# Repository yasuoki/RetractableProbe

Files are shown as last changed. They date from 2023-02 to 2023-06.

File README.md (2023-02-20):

# Retractable probe built into X-carriage
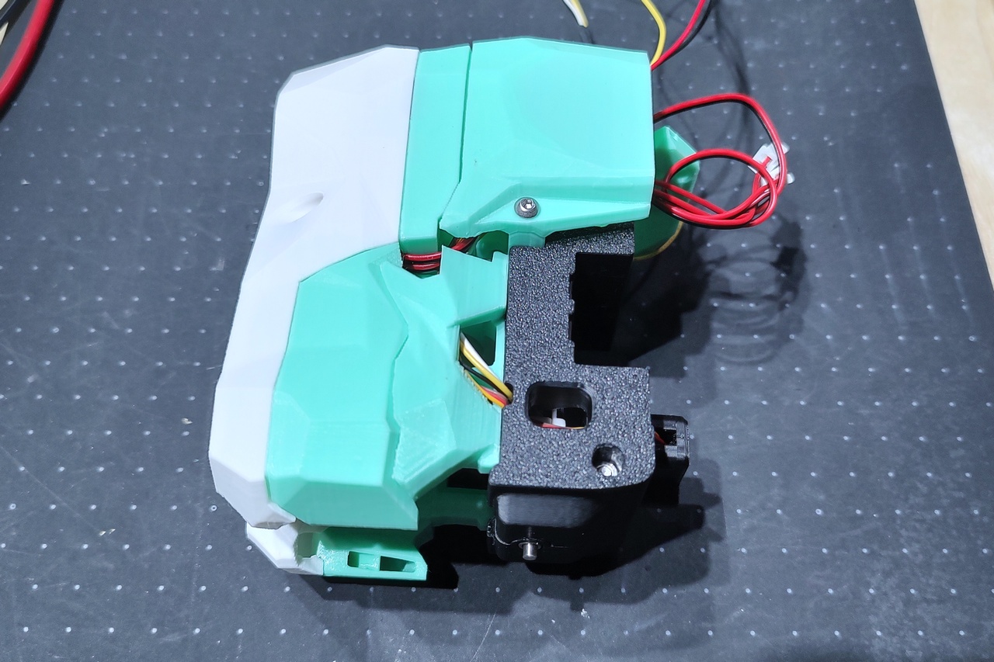
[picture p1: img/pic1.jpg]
<br>

(https://www.youtube.com/watch?v=CPbT1QPZcho)

The retractable probe of the Strix toolhead has been miniaturized and integrated into the X-carriage.  
The project features the following.

- Fits MGN12 X-rail only
- Replaces OMRON TL-Q5MC, which has concerns about heat resistance.
- Same size as the genuine VORON X-Carriage, so AfterBurner and StealthBurner can be used.
- Same weight as the genuine VORON X-Carriage with OMRON TL-Q5MC.
- Robust electrical circuits with no magnet-dependent electrical contacts.
- The accuracy of the probe depends only on the accuracy of the microswitch and not on the servomotor or spring.

# Caution
This probe is still under development and has not yet been tested for stability.   
I am trying to design a better, but something could go wrong and your 3D printer could break.

# BOM
- M3 x 30mm SHCS x1
- M3 x 40mm SHCS x1
- M2x10 Self Tapping Screw x4
- M1.7 x 3mm Flat Head Screw x1 (for servo horn)
- M3 x 6mm Set Screw x1
- M3 Hexnut x2
- M3 Heat Set Inserts x4
- Piano wire 0.8mm(D) x 6mm(L) x1
- Sleeve Bearing(Oilless Bushings) 3mm(ID) x 5mm(OD) x 5mm(L) x4
- Stainless Steel Compression Spring 4mm(OD) x 0.4mm(RD) x 15mm(L) x1
- Stainless Steel Shaft 3mm(D) x 57mm(L) x1
- E-Clip 2.0~2.5mm(ID) x2
- Wire 32~36AWG
- Micro Switch (OMRON D2F-01F Low operating force 0.74 N) x1
- Servo Motor (Dspower DS-M005) x1

LED Options
- LED Blue 3mm x1
- LED Red 3mm x1
- Resistor 1/4W 330~2k ohms x2 (Resistance depends on circuit)

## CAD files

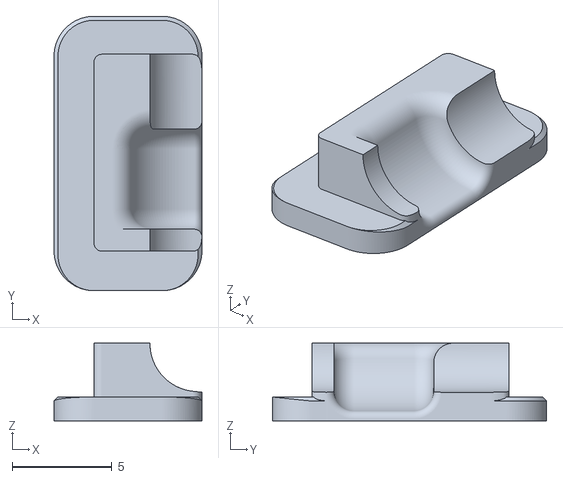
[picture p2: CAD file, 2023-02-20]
STLs/CableHoleLid.stl
7.40 x 13.7 x 3.89

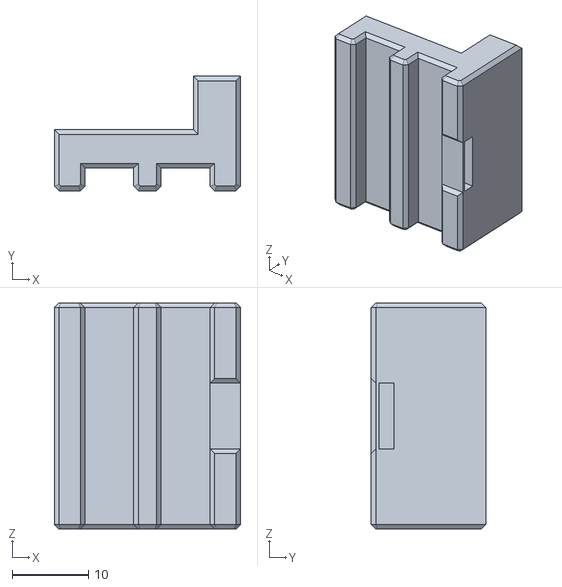
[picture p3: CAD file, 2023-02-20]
STLs/Tools/BeltGuideB_x2.stl
24.4 x 15.0 x 29.6

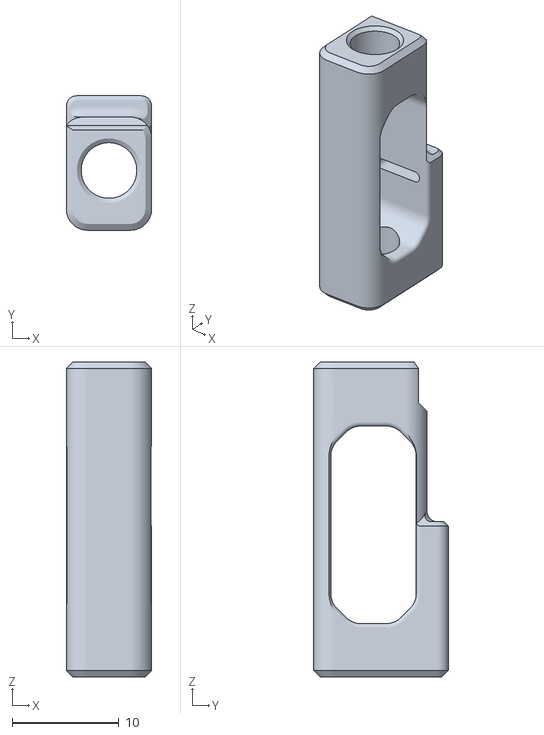
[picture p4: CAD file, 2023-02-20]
STLs/Elevator.stl
8.00 x 12.6 x 29.5

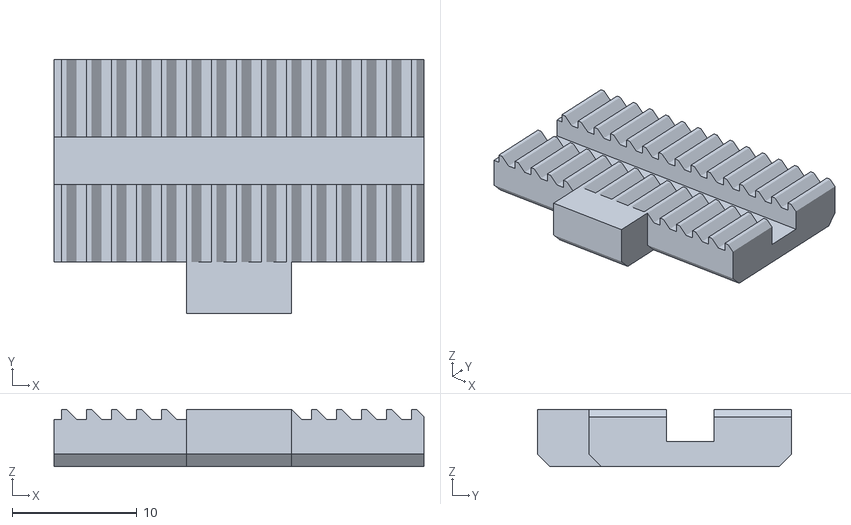
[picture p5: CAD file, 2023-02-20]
STLs/Tools/BeltGuideR.stl
29.6 x 20.3 x 4.60

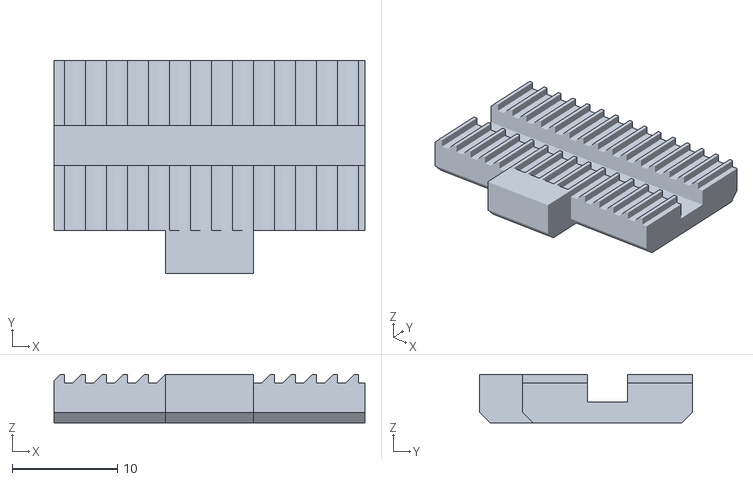
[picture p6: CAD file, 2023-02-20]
STLs/Tools/BeltGuideL.stl
29.6 x 20.3 x 5.00

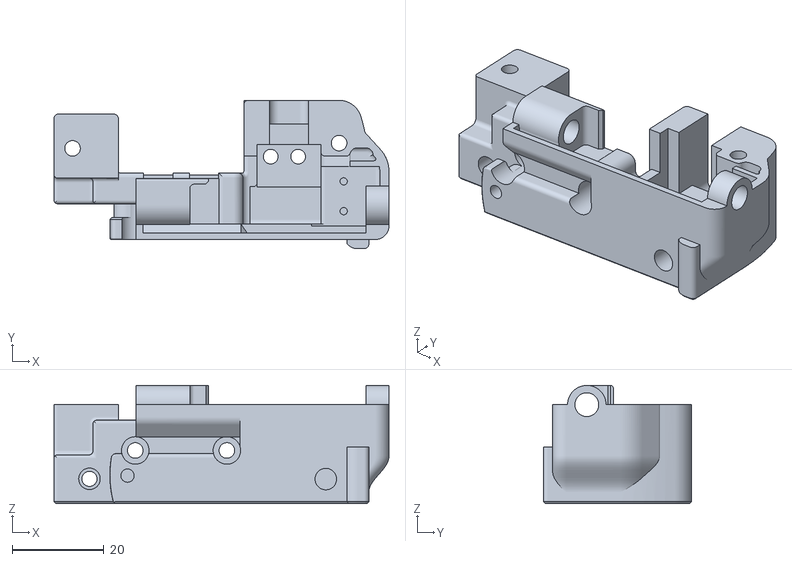
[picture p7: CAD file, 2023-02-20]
STLs/XCarriageLeft.stl
73.1 x 32.4 x 25.8

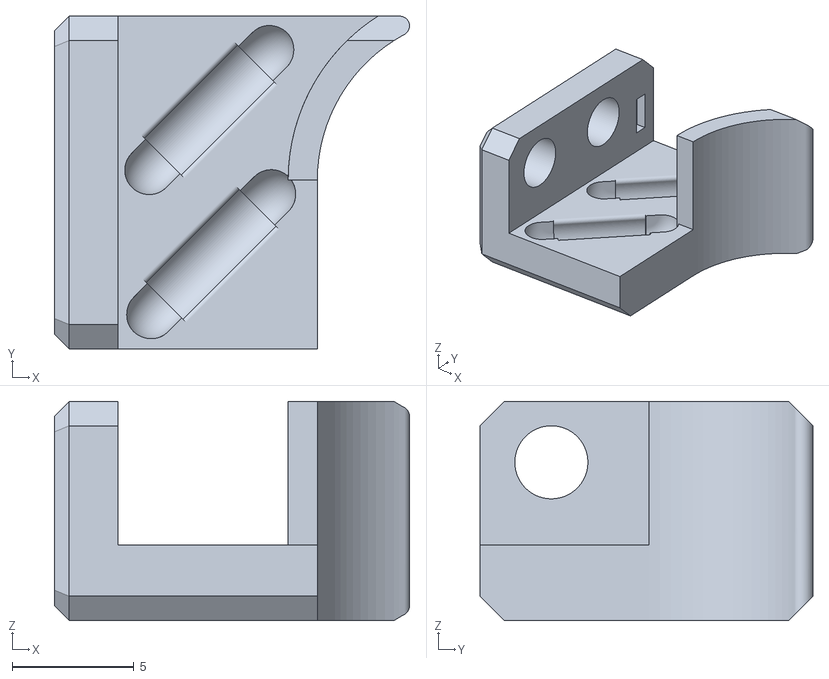
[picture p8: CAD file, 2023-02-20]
STLs/LedMount.stl
14.6 x 13.7 x 9.00

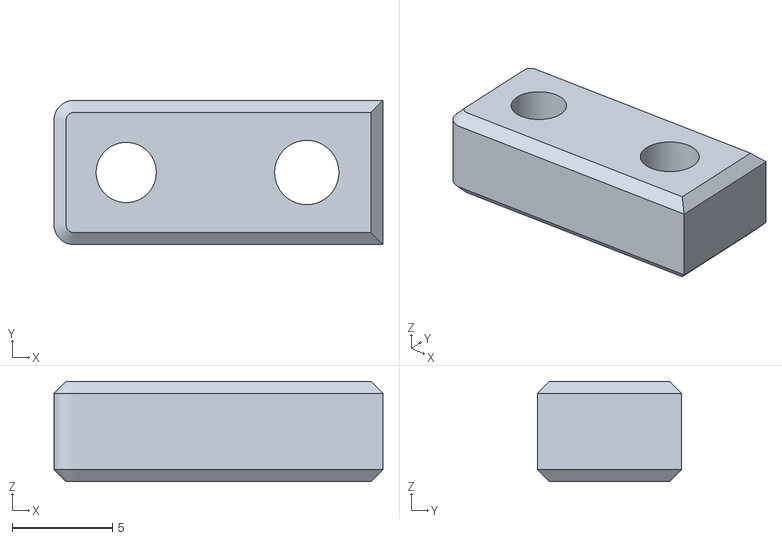
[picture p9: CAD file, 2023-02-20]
STLs/Trigger.stl
16.4 x 7.20 x 5.00

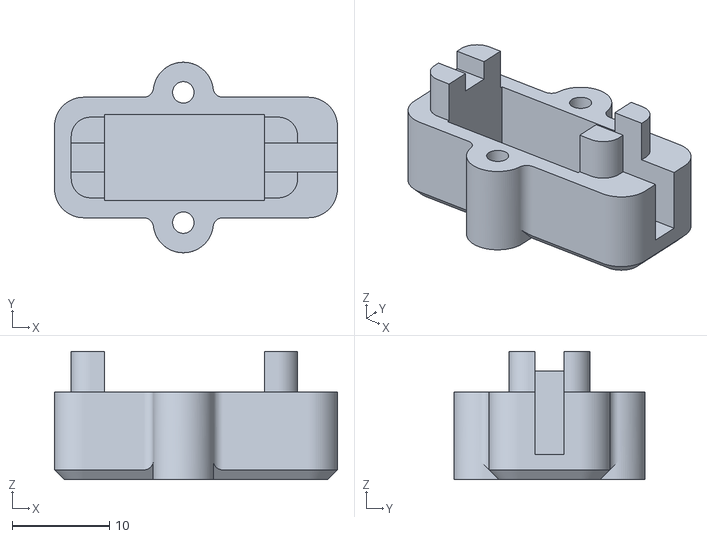
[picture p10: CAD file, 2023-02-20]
STLs/ServoCover.stl
29.1 x 19.6 x 13.2

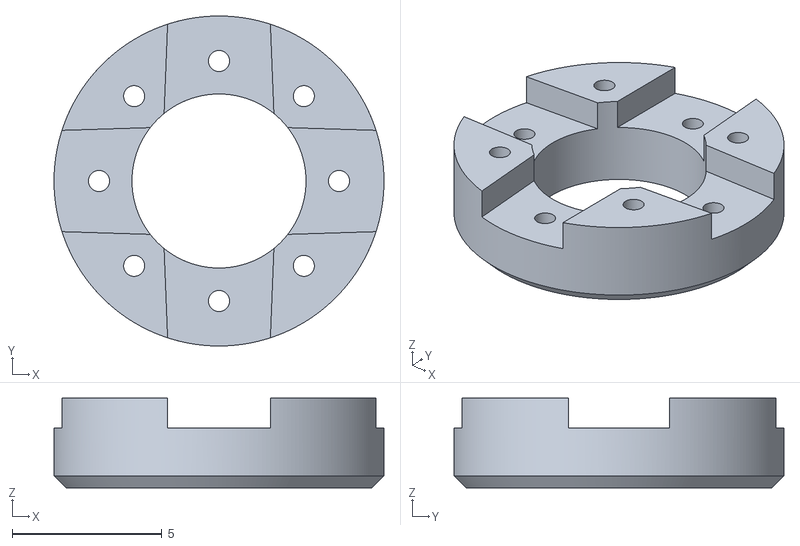
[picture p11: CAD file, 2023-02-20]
STLs/ServoHornA.stl
11.0 x 11.0 x 3.00

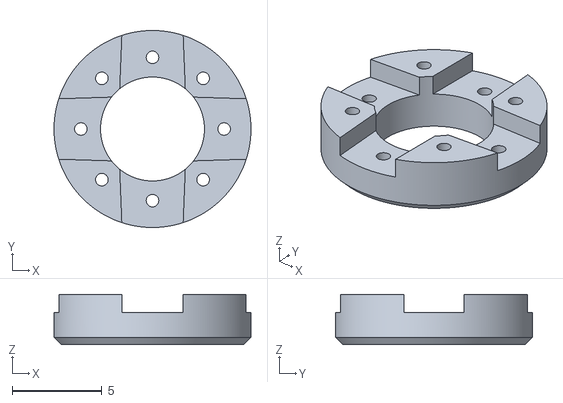
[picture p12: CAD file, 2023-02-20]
STLs/ServoHornB.stl
11.0 x 11.0 x 2.80

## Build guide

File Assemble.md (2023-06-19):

## Wiring for LEDs
This manual does NOT describe the wiring of LEDs.  
The reason is that additional circuitry and motherboard configuration are required to turn on the LEDs, and various configurations are possible depending on the individual printer environment.  
The design is intended to allow for LED installation, but it is not required. If you think it is necessary, please devise your own wiring.  
A simplified schematic is shown below, but the question is where to wire the 3.3V from?  
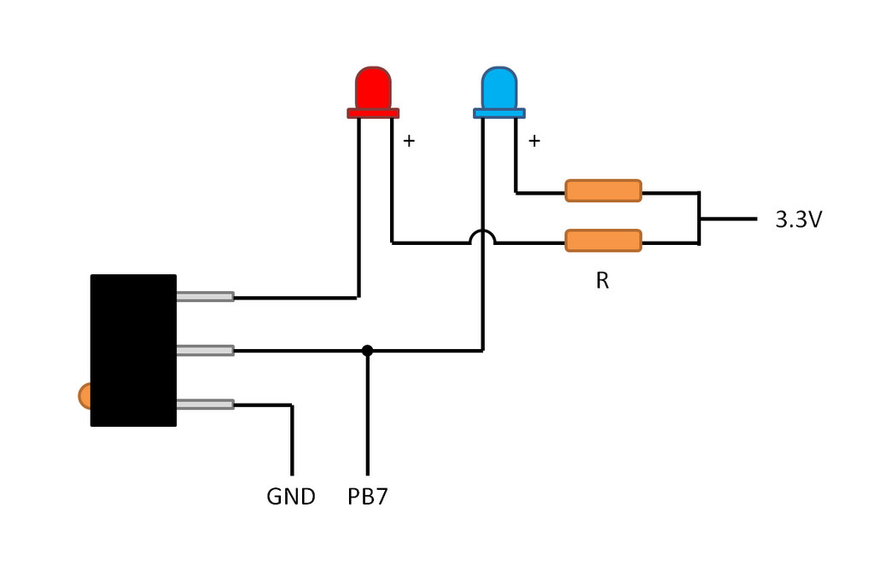
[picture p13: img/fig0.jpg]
<br>  
This 3.3V needs to be controllable by G-Code as I want to turn it on and off in conjunction with probe rod expansion and retraction.  
From what I have seen in the BTT Octopus schematic, it looks like the only PINs that can be used for such an application are probably Fan0-Fan5 (Fan6 and 7 cannot be used), or J37 for the Neopixel LED.  
Both PINs are 5v or higher, so to obtain 3.3V, either a step-down by regulator or leveling PWM output is required.  

## Parts Printing
Layer height 0.2mm, Extrusion width 0.4mm, Wall count 4, Top/Bottom layers 8, Infill 40%.  
All parts do not require support.  
Some parts have built-in supports, so remove them.  
ServoHornA.stl and ServoHornB.stl differ in thickness by 0.2 mm. Select the one that fits.  

## Assemble
Only procedures different from the VORON standard X-Cariagge are explained.  
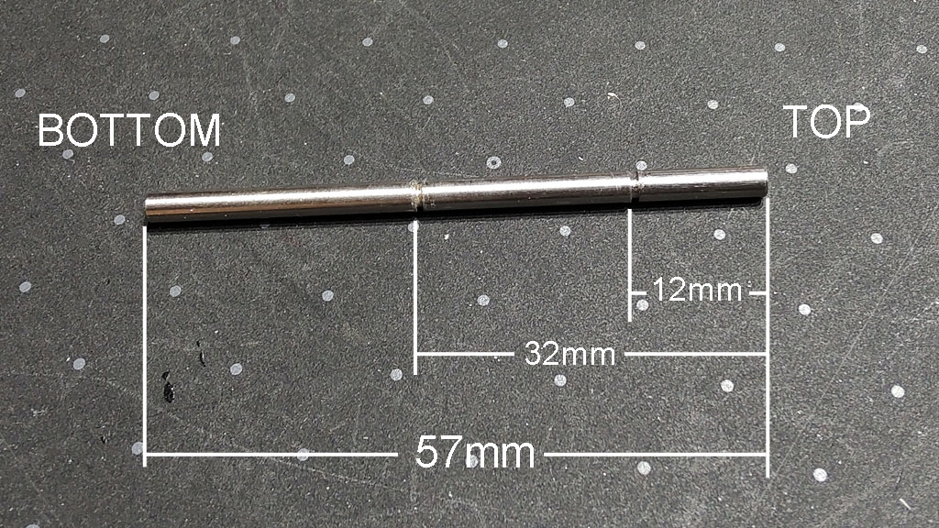
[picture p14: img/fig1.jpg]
<br>
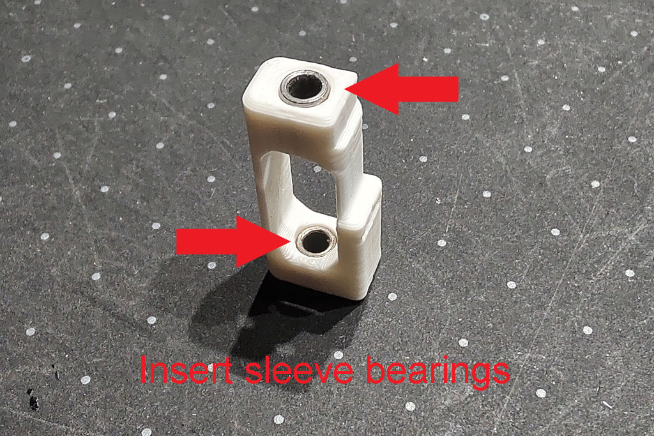
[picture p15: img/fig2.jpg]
<br>
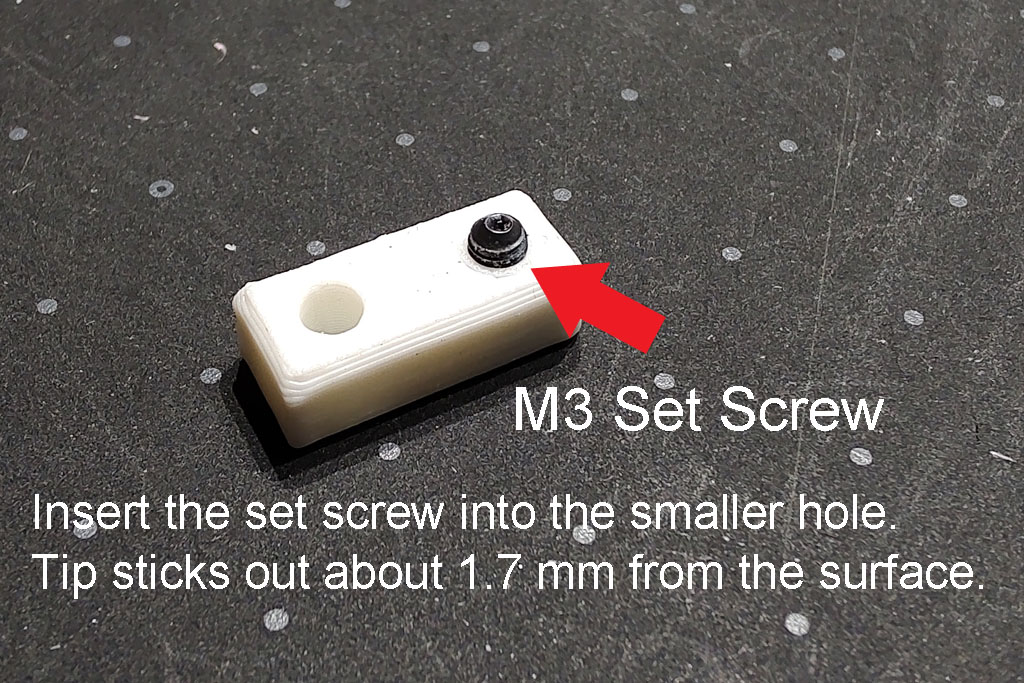
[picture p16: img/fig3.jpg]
<br>
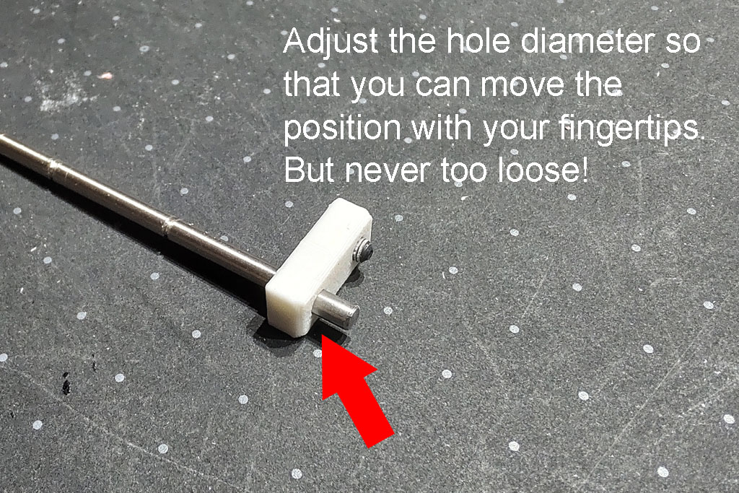
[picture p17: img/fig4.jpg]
<br>
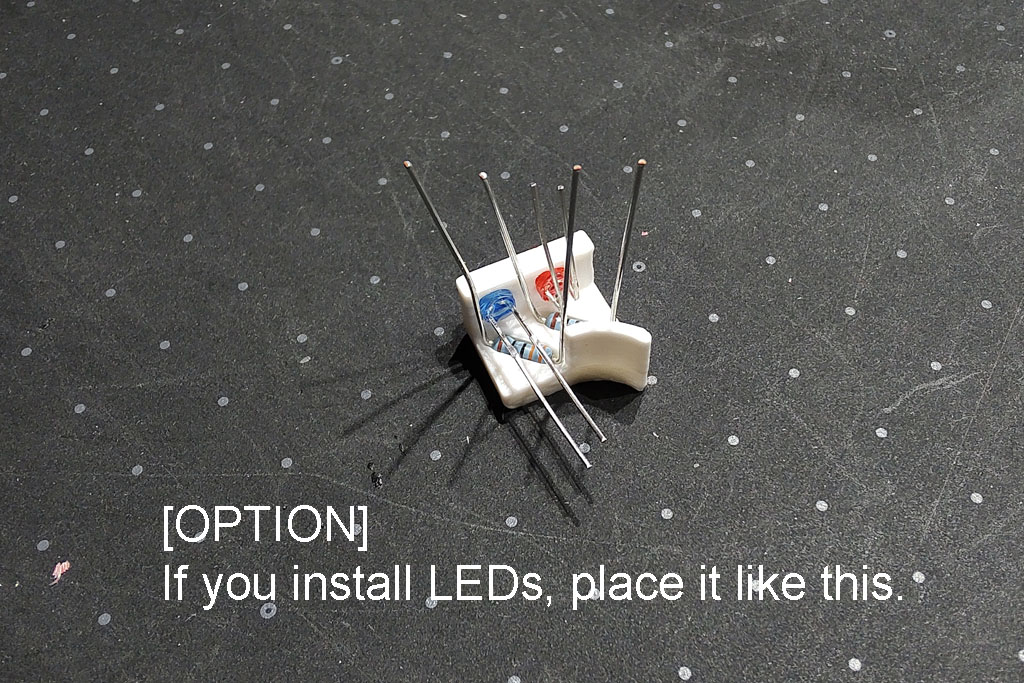
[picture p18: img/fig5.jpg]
<br>
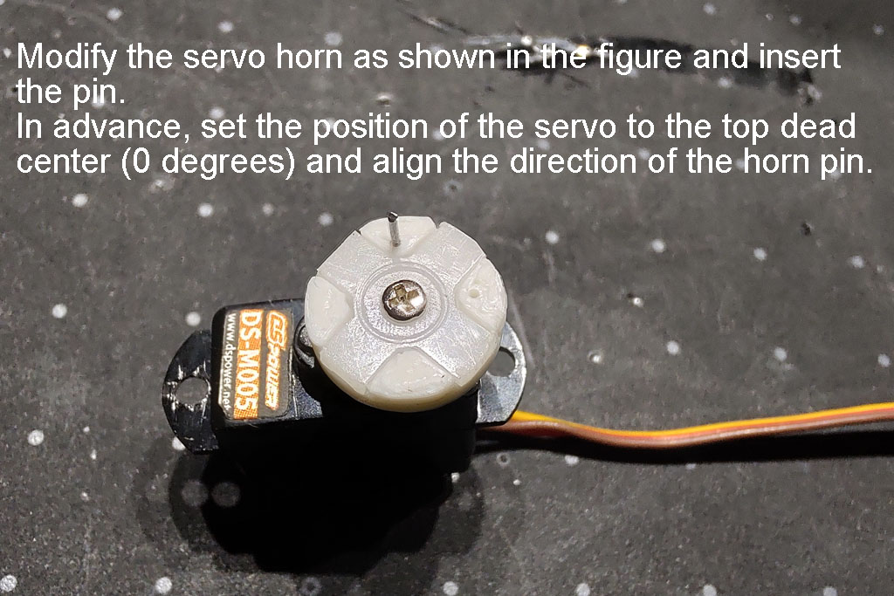
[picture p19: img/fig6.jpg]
<br>
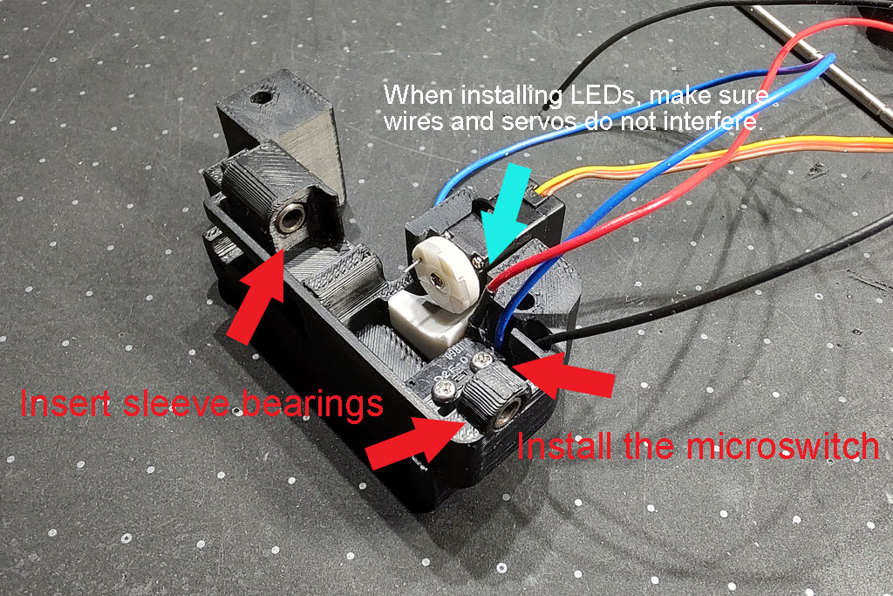
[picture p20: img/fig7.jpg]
<br>
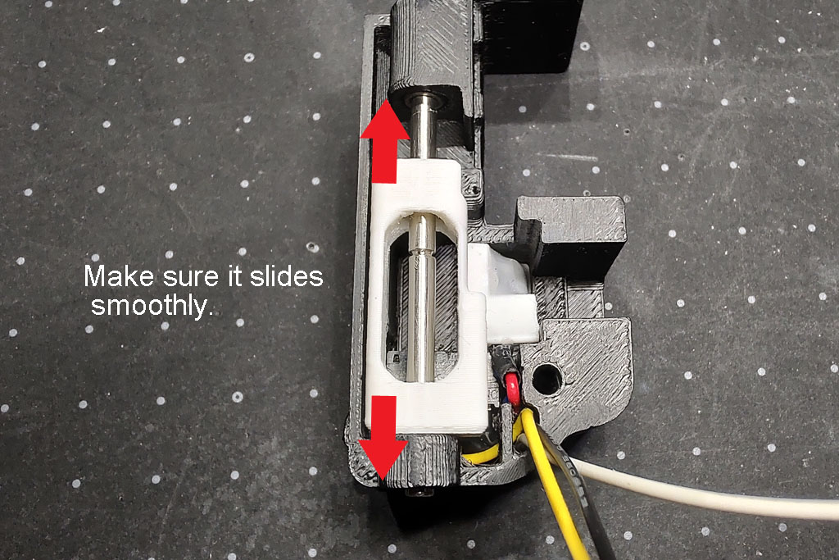
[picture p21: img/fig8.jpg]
<br>
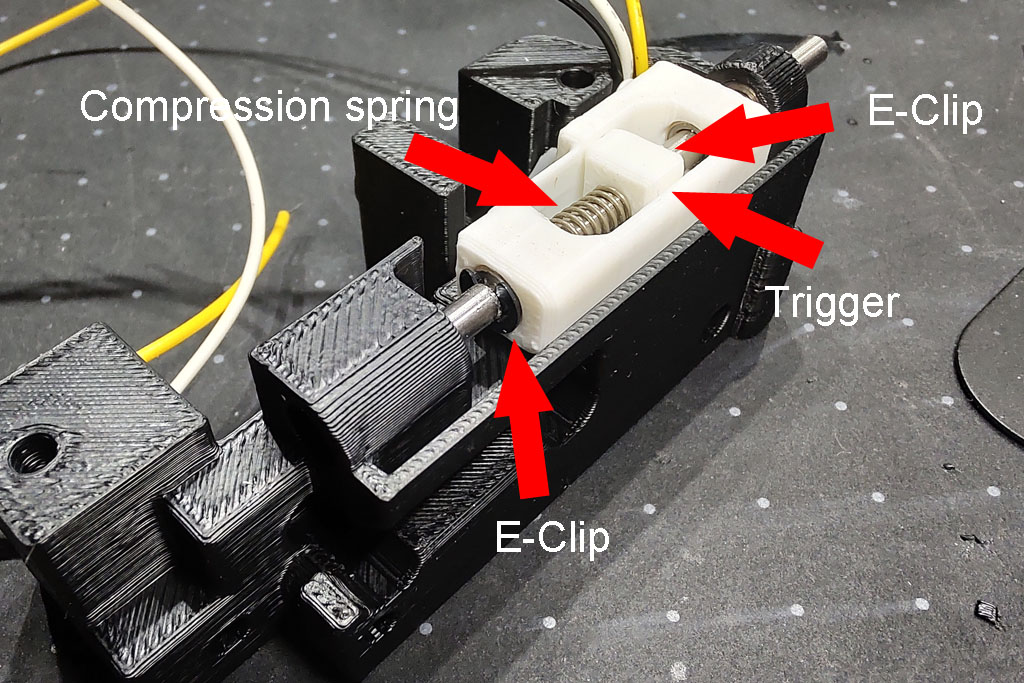
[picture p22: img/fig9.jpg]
<br>
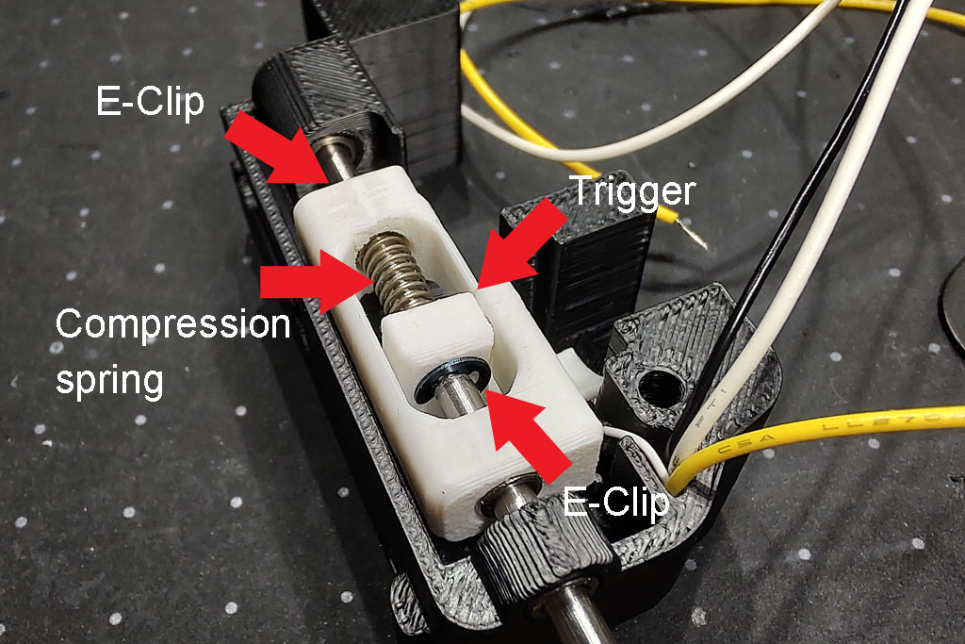
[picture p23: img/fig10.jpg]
<br>
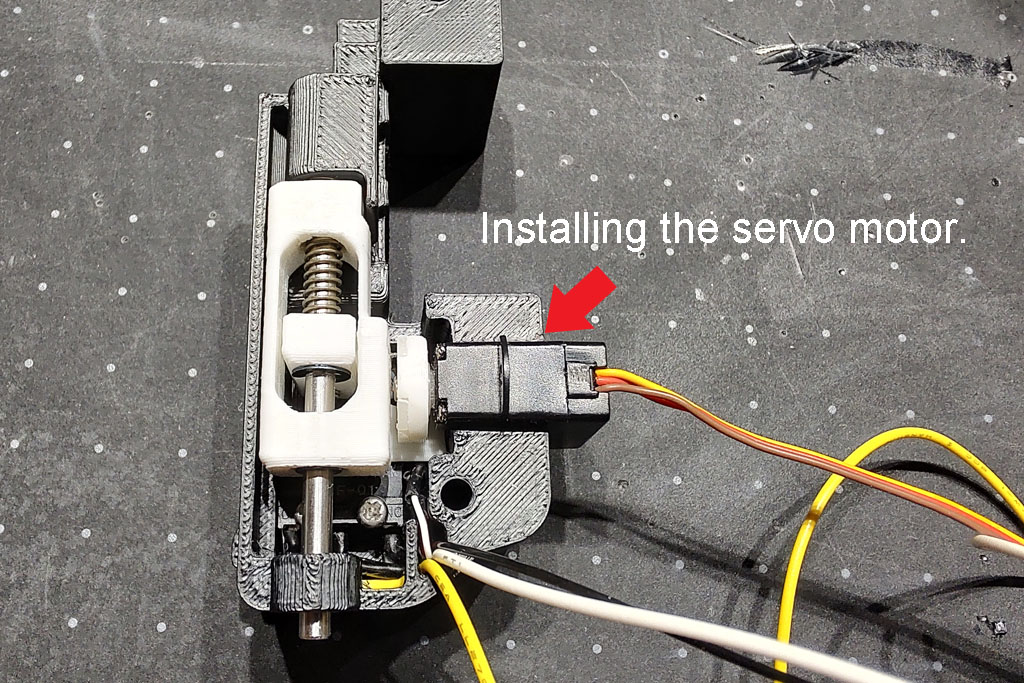
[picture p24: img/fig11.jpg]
<br>
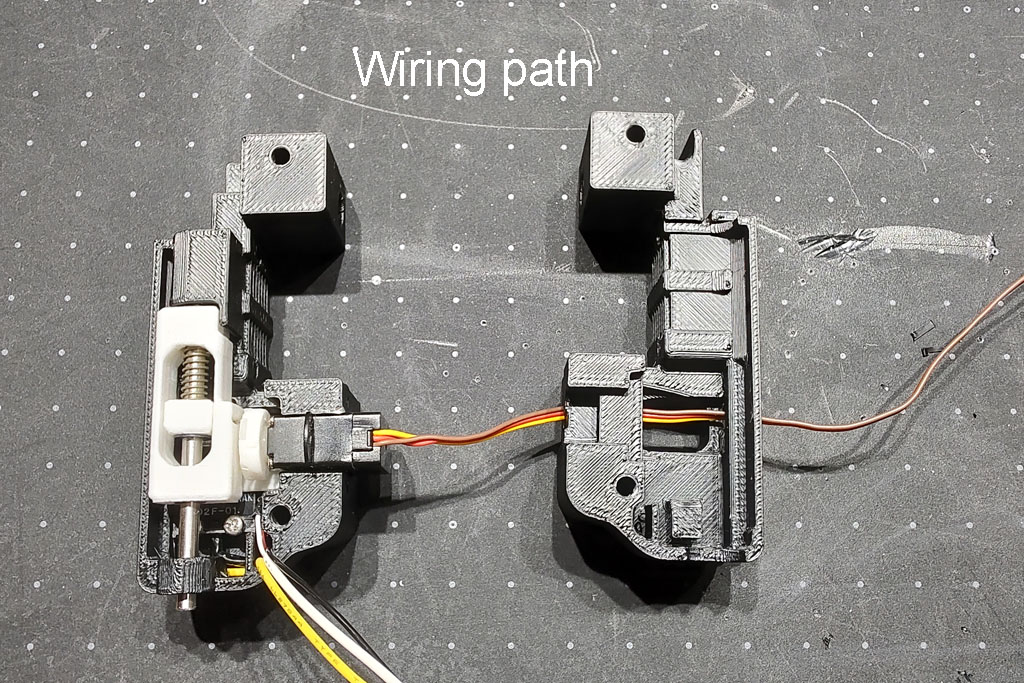
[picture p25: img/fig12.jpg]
<br>
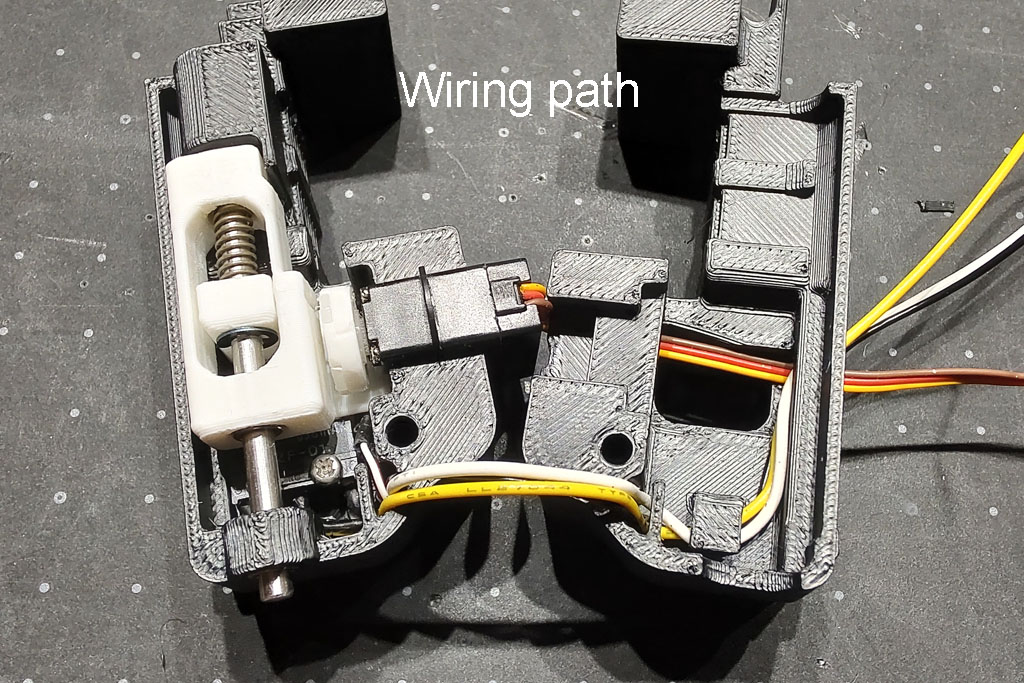
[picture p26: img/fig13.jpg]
<br>
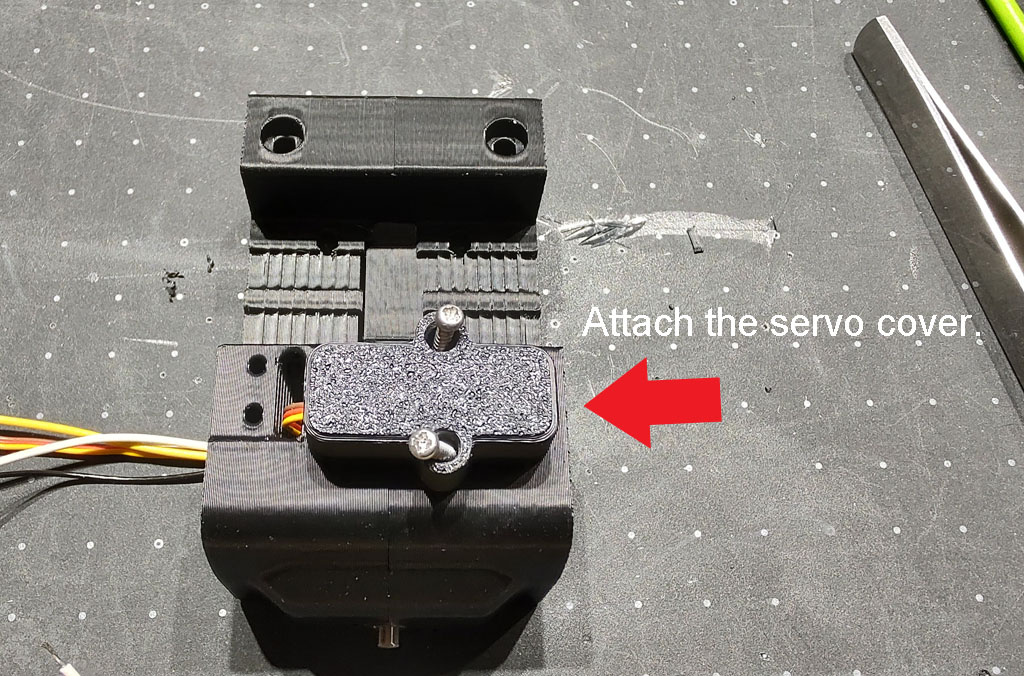
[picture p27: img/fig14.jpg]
<br>
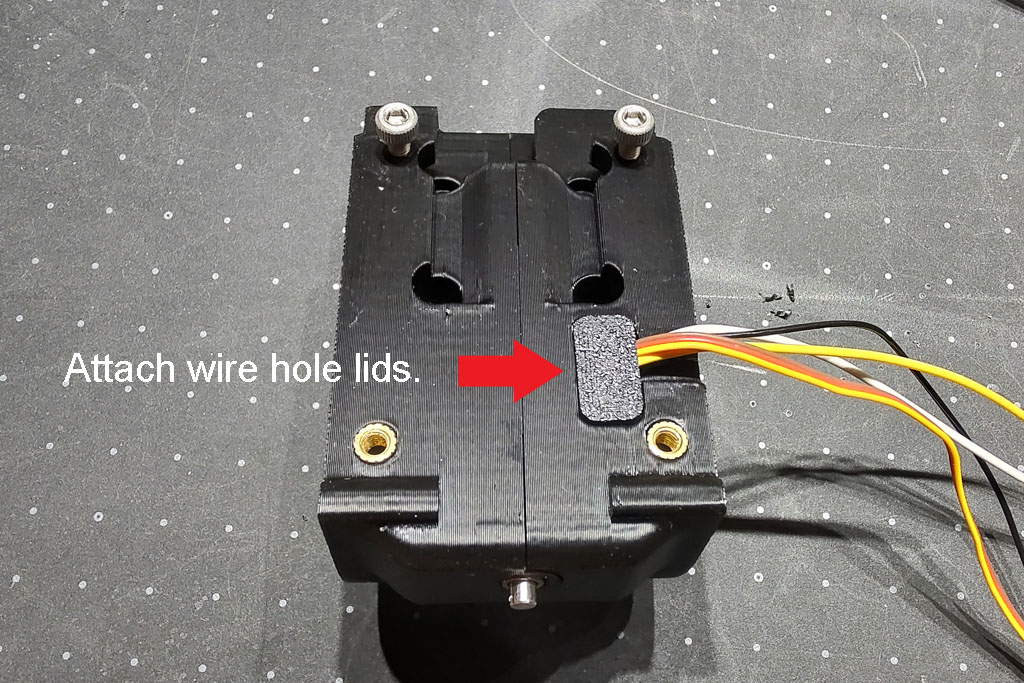
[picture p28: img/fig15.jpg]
<br>

## Mounting on the X-axis
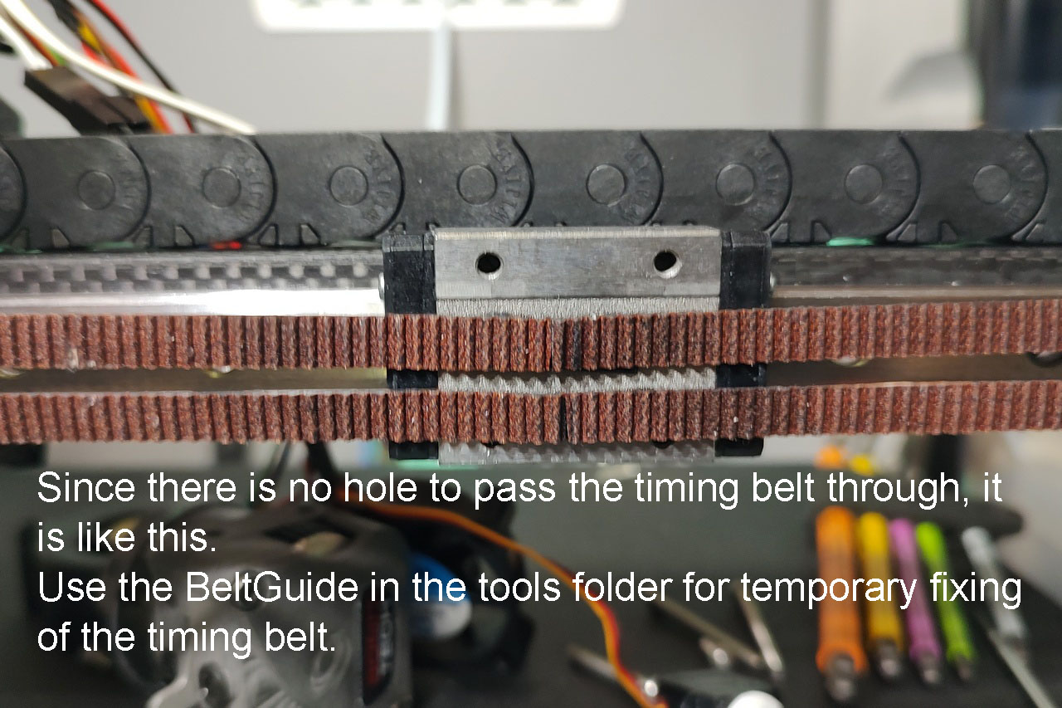
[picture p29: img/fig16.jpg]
<br>

## Wirering
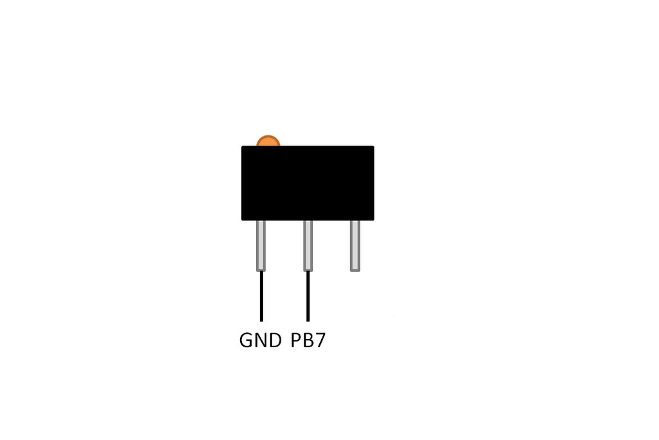
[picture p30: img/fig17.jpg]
<br>
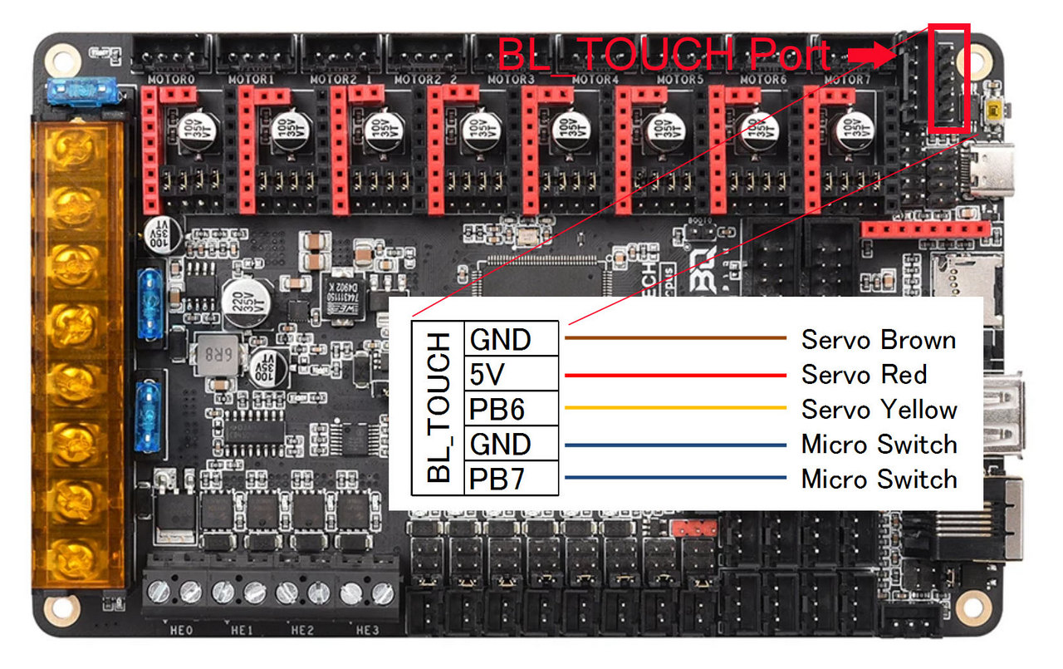
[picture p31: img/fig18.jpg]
<br>

## Configuration (sample)
~~~
#####################################################################
#   Retractable Probe Servo
#####################################################################
[servo RetractableProbe]
pin: PB6
initial_angle: 0
maximum_servo_angle = 180
minimum_pulse_width = 0.0005
maximum_pulse_width = 0.0024

[gcode_macro PROBE_OUT]
gcode:
    SET_SERVO SERVO=RetractableProbe ANGLE=180
    G4 P800

[gcode_macro PROBE_IN]
gcode:
    SET_SERVO SERVO=RetractableProbe ANGLE=0
    SET_SERVO SERVO=RetractableProbe WIDTH=0
    G4 P800

#####################################################################
#   Probe
#####################################################################
[probe]
pin: ^PB7
x_offset: 0
y_offset: 25.0
z_offset: 0
speed: 10.0
samples: 3
samples_result: median
sample_retract_dist: 3.0
samples_tolerance: 0.006
samples_tolerance_retries: 3
deactivate_on_each_sample: False
activate_gcode:
    PROBE_OUT
deactivate_gcode:
    PROBE_IN
~~~
